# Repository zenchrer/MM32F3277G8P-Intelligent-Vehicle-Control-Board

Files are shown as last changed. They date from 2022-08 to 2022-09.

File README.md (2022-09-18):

# MM32F3277G8P-Intelligent-Vehicle-Control-Board

## 已添加[Sbus解析例程](https://github.com/zenchrer/MM32-Sbus-Demo.git)<br>
8/31/2022 9:24:01 PM <br>
&nbsp;&nbsp;&nbsp;&nbsp;本项目是2022年全国大学生智能车竞赛平衡信标组桂林信息科技学院Tornado(队)的硬件开源;
在一块PCB上集成了电机驱动以及其它外设接口,基本满足平衡信标组的功能需求,引脚大部分兼容某飞科技的开源程序,某飞的代码虽然有些BUG,但是大体方便可靠(个人认为比隔壁lq的好);电源部分设计参考了2021年立创开源广场moximoxi大佬的开源硬件:[传送门](https://oshwhub.com/moximoxi/shuang-jum3_mini)<br>

***
### 主要特点
+ 主控采用了灵动微电子MM32F3277G8P作为MCU;<br>
+ 电机驱动使用之前开源的EG3013栅极驱动以及N-Channel Mosfet;<br>
+ 预留S-bus接口,方便老车退役改成遥控车;(bushi)<br>
+ 预留并口屏,理论上相比SPI屏幕刷新更快,节约CPU时间;
+ 使用开源EDA软件Kicad6.0.2绘制;
***
### 开发者
组织：桂林信息科技学院 通信创新实践基地<br>
作者：zenchrer [邮箱](zenchrer@qq.com)
***

### 外观
PCB正面

安装图

安装图
***

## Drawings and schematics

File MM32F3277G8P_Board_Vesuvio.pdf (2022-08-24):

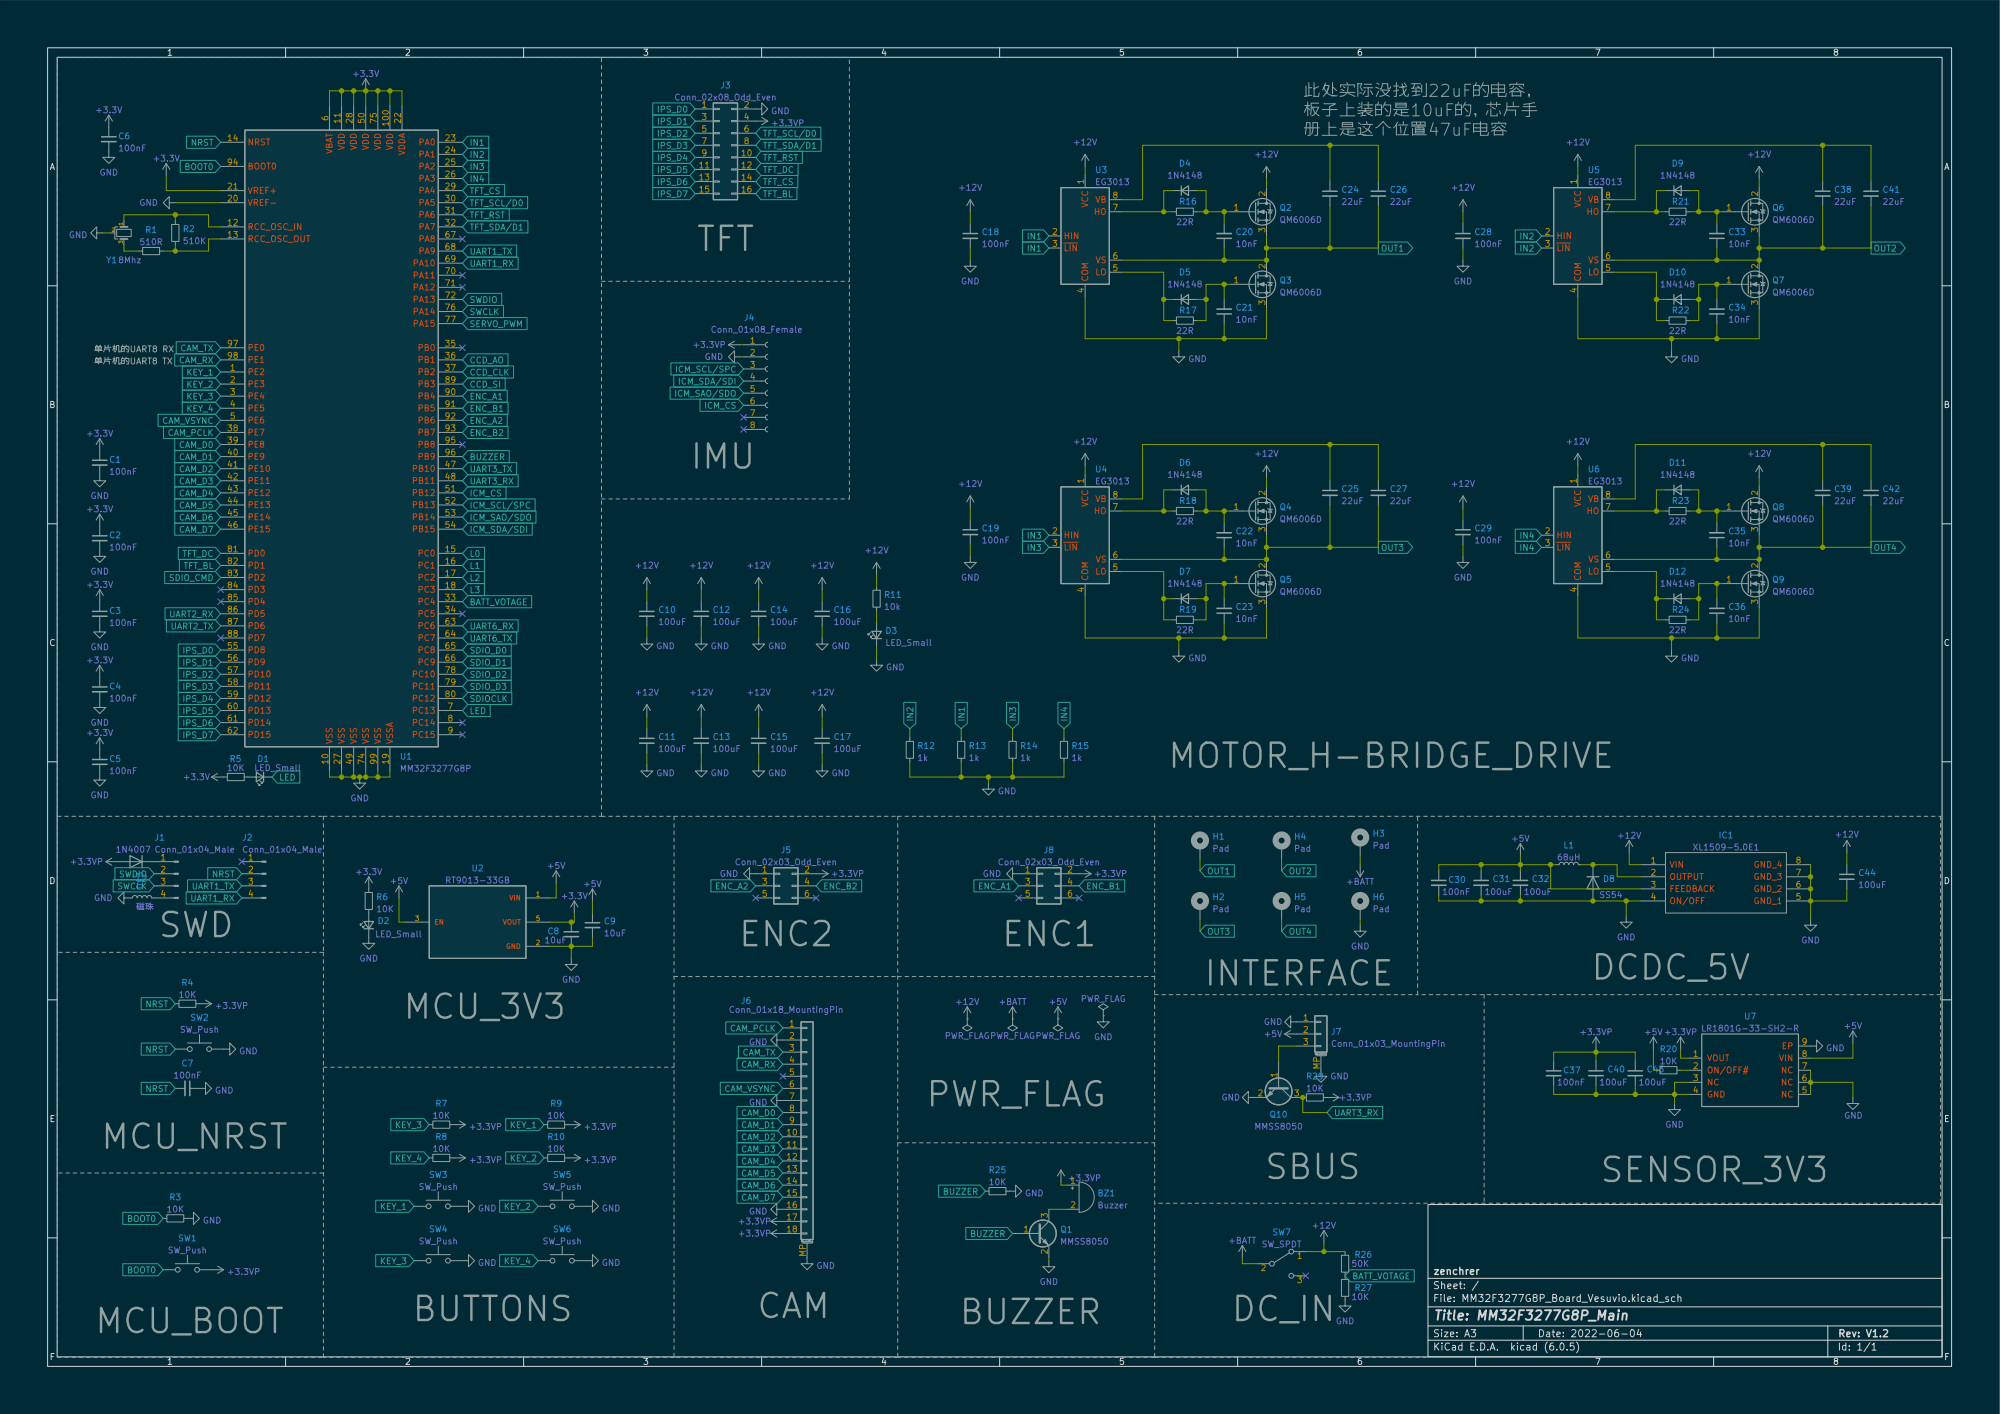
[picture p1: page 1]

þÿkdY[ž–El¡b~R022uFv„u5[¹ÿ þÿg•[PN

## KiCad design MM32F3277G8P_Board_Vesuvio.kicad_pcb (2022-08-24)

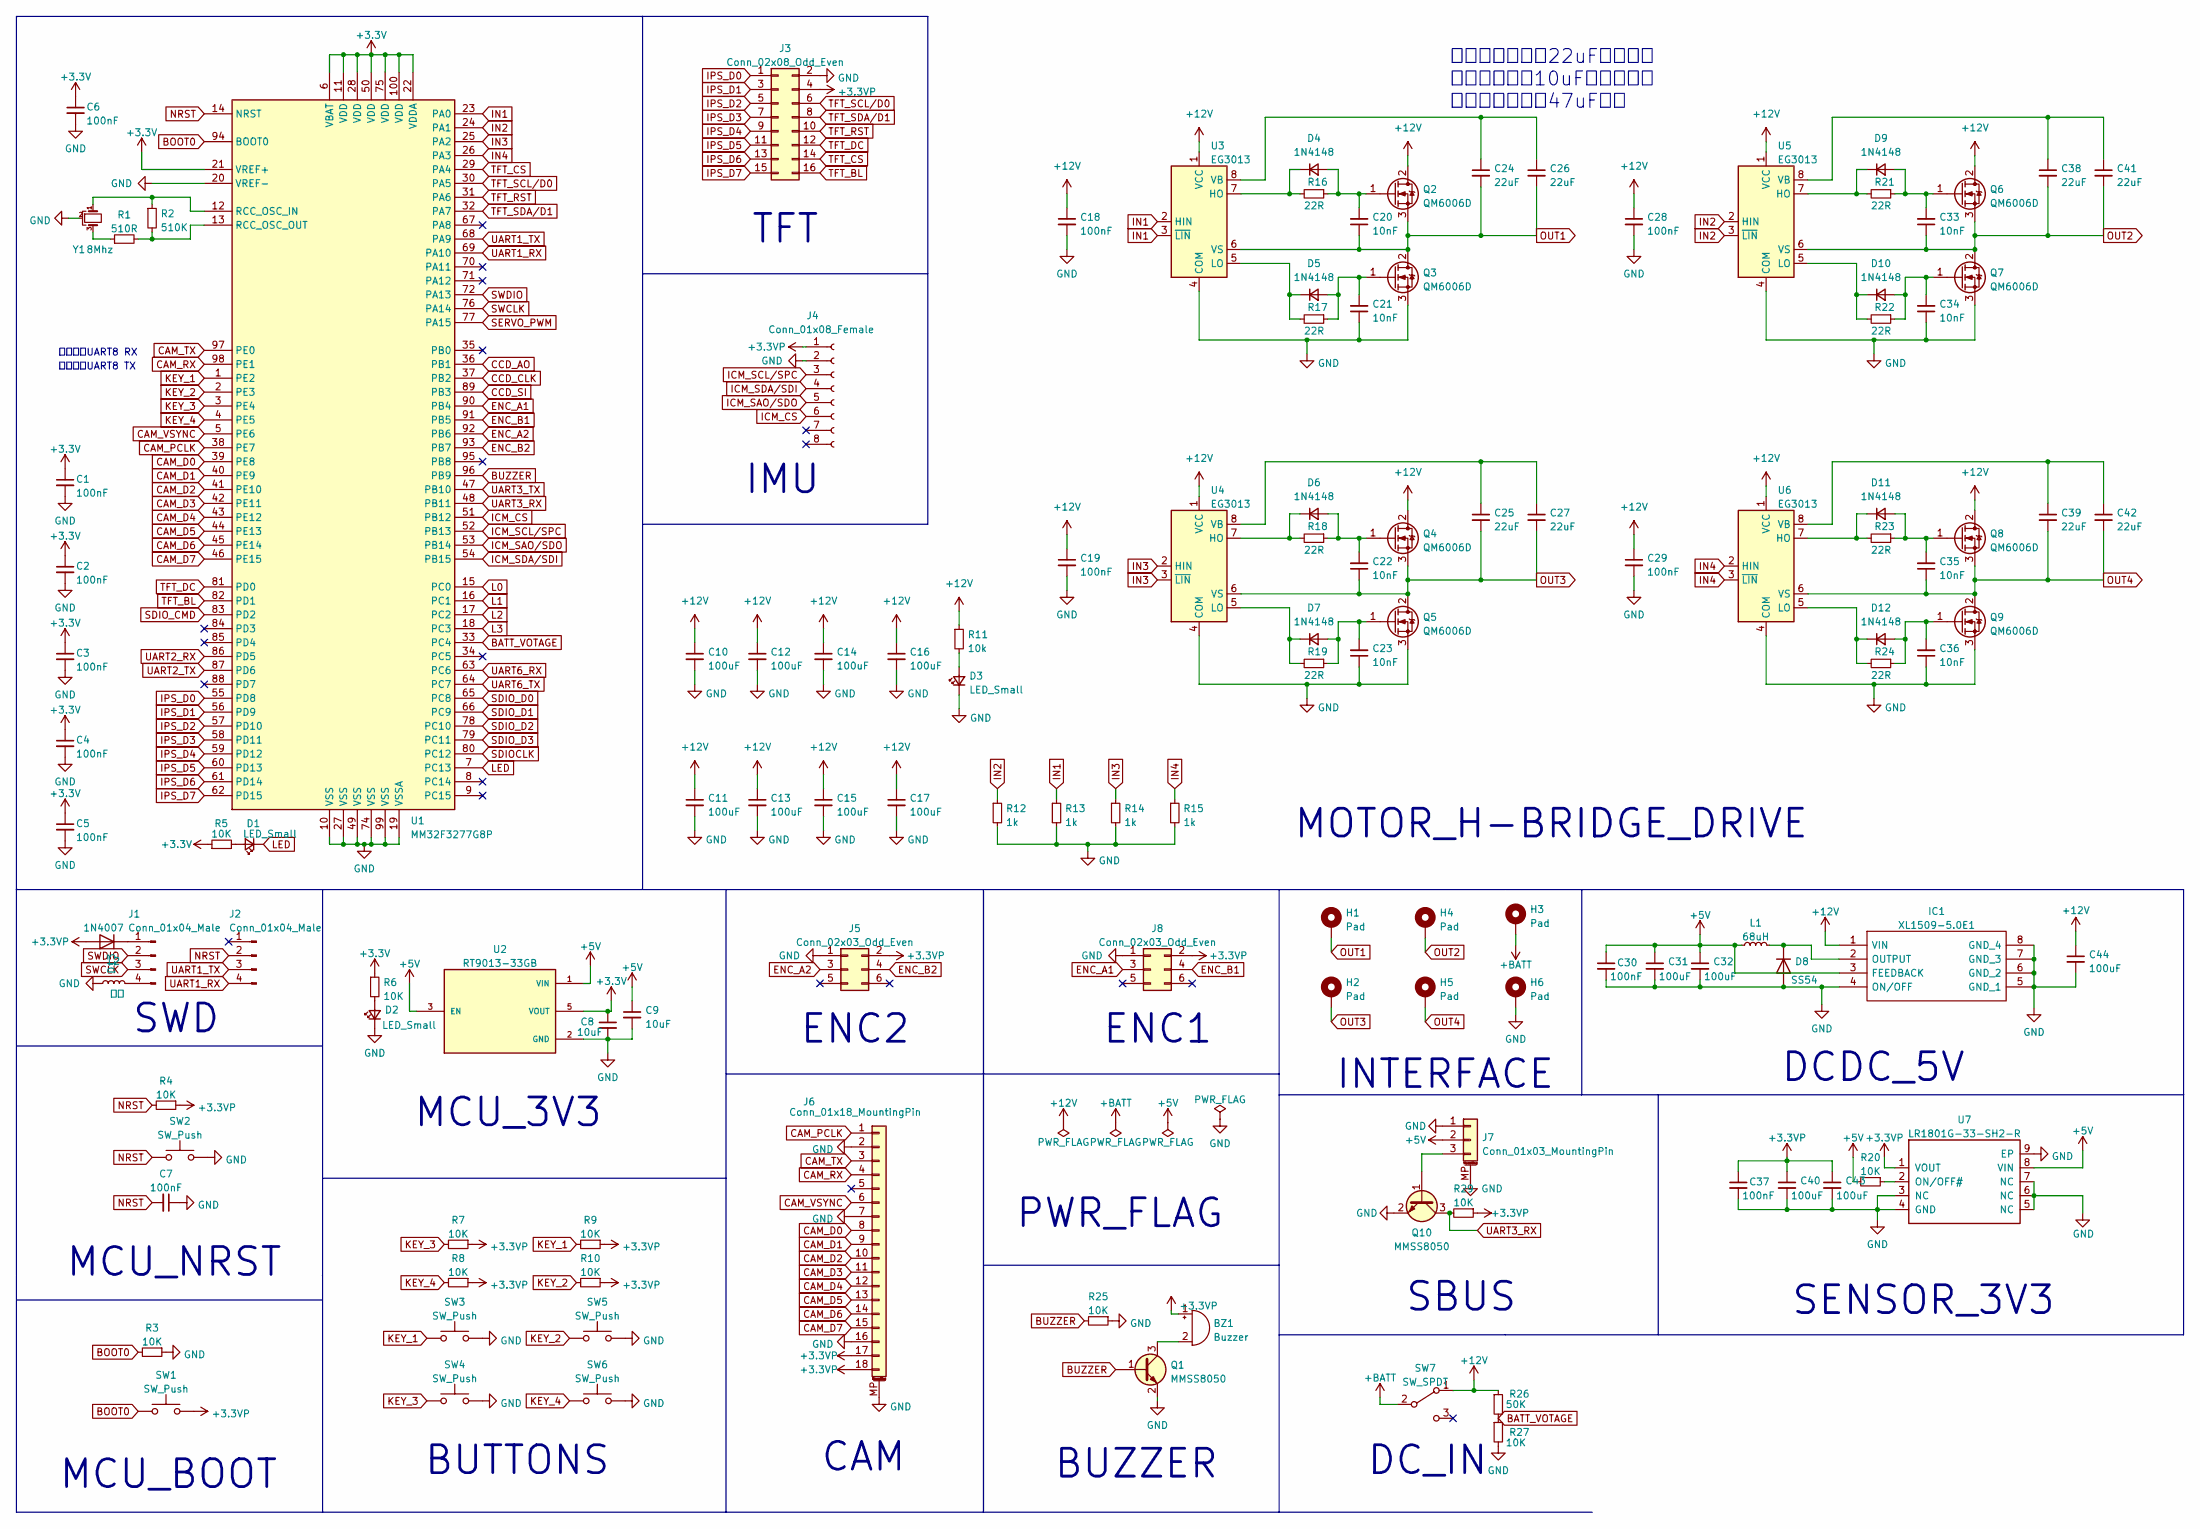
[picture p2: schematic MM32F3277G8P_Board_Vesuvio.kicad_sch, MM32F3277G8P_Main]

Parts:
BZ1: Buzzer; MagneticBuzzer_PUI_AT-0927-TT-6-R
C1, C2, C3, C4, C5, C6, C7, C18, C19, C28, C29, C30, C37: 100nF; C_0603_1608Metric
C8, C9: 10uF; C_0805_2012Metric
C10, C11, C12, C13, C14, C15, C16, C17, C31, C32, C40, C43, C44: 100uF; C_1210_3225Metric
C20, C21, C22, C23, C33, C34, C35, C36: 10nF; C_0402_1005Metric
C24, C25, C26, C27, C38, C39, C41, C42: 22uF; C_0805_2012Metric
D1, D2, D3: LED_Small; LED_0603_1608Metric
D4, D5, D6, D7, D9, D10, D11, D12: 1N4148; D_SOD-123
D8: SS54; D_SMA
D13: 1N4007; D_SMA
H1, H2, H4, H5: Pad; MountingHole_2.2mm_M2_Pad_Via
H3, H6: Pad; MountingHole_2.5mm_Pad_Via
IC1: XL1509-5.0E1; SOIC-8_3.9x4.9mm_P1.27mm; Manufacturer_Part_Number XL1509-5.0E1
J1, J2: Conn_01x04_Male; PinHeader_1x04_P2.54mm_Vertical
J3: Conn_02x08_Odd_Even; PinHeader_2x08_P2.54mm_Vertical
J4: Conn_01x08_Female; PinHeader_1x08_P2.54mm_Vertical
J5, J8: Conn_02x03_Odd_Even; IDC-Header_2x03_P2.54mm_Vertical
J6: Conn_01x18_MountingPin; TE_1-1734839-8_1x18-1MP_P0.5mm_Horizontal
J7: Conn_01x03_MountingPin; JST_SH_SM03B-SRSS-TB_1x03-1MP_P1.00mm_Horizontal
L1: 68uH; L_7.3x7.3_H3.5
L2: 磁珠; Fuse_0805_2012Metric
Q1, Q10: MMSS8050; SOT-23
Q2, Q3, Q4, Q5, Q6, Q7, Q8, Q9: QM6006D; TO-252-2
R1: 510R; R_0603_1608Metric
R2: 510K; R_0603_1608Metric
R3, R4, R5, R6, R7, R8, R9, R10, R20, R25, R27, R29: 10K; R_0603_1608Metric
R11: 10k; R_0603_1608Metric
R12, R13, R14, R15: 1k; R_0603_1608Metric
R16, R17, R18, R19, R21, R22, R23, R24: 22R; R_0402_1005Metric
R26: 50K; R_0603_1608Metric
SW1, SW2, SW3, SW4, SW5, SW6: SW_Push; SW_SPST_PTS810
SW7: SW_SPDT; MTS102
U1: MM32F3277G8P; LQFP-100_14x14mm_P0.5mm
U2: RT9013-33GB; SOT-23-5; PARTREV Aprill 2011
U3, U4, U5, U6: EG3013; SOIC-8_3.9x4.9mm_P1.27mm
U7: LR1801G-33-SH2-R; HSOP-8-1EP_3.9x4.9mm_P1.27mm_EP2.3x2.3mm_ThermalVias
Y1: 8Mhz; Resonator_SMD_Murata_CSTxExxV-3Pin_3.0x1.1mm

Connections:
+3.3VP: BZ1.1 (-), C37.1, C40.1, C43.1, D13.2 (A), J3.4, J4.1, J5.2, J6.17, J6.18, J8.2, R4.1, R7.1, R8.1, R9.1, R10.1, R29.1, SW1.2, U7.1 (VOUT)
+3V3: C1.1, C2.1, C3.1, C4.1, C5.1, C6.1, C8.1, R5.1, R6.1, U1.6 (VBAT), U1.11 (VDD), U1.21 (VREF+), U1.22 (VDDA), U1.28 (VDD), U1.50 (VDD), U1.75 (VDD), U1.100 (VDD), U2.5 (VOUT)
+5V: C9.1, C30.1, C31.1, C32.1, IC1.3 (FEEDBACK), J7.2, L1.1, R20.2, U2.1 (VIN), U2.3 (EN), U7.8 (VIN)
+12V: C10.1, C11.1, C12.1, C13.1, C14.1, C15.1, C16.1, C17.1, C18.1, C19.1, C28.1, C29.1, C44.1, IC1.1 (VIN), Q2.2 (D), Q4.2 (D), Q6.2 (D), Q8.2 (D), R11.1, R26.1, SW7.1 (A), U3.1 (VCC), U4.1 (VCC), U5.1 (VCC), U6.1 (VCC)
+BATT: H3.1, SW7.2 (B)
BATT_VOTAGE: R26.2, R27.1, U1.33 (PC4)
BOOT0: R3.2, SW1.1, U1.94 (BOOT0)
BUZZER: Q1.1 (B), R25.2, U1.96 (PB9)
CAM_D0: J6.8, U1.39 (PE8)
CAM_D1: J6.9, U1.40 (PE9)
CAM_D2: J6.10, U1.41 (PE10)
CAM_D3: J6.11, U1.42 (PE11)
CAM_D4: J6.12, U1.43 (PE12)
CAM_D5: J6.13, U1.44 (PE13)
CAM_D6: J6.14, U1.45 (PE14)
CAM_D7: J6.15, U1.46 (PE15)
CAM_PCLK: J6.1, U1.38 (PE7)
CAM_RX: J6.4, U1.98 (PE1)
CAM_TX: J6.3, U1.97 (PE0)
CAM_VSYNC: J6.6, U1.5 (PE6)
CCD_AO: U1.36 (PB1)
CCD_CLK: U1.37 (PB2)
CCD_SI: U1.89 (PB3)
ENC_A1: J8.3, U1.90 (PB4)
ENC_A2: J5.3, U1.92 (PB6)
ENC_B1: J8.4, U1.91 (PB5)
ENC_B2: J5.4, U1.93 (PB7)
GND: C1.2, C2.2, C3.2, C4.2, C5.2, C6.2, C7.1, C8.2, C9.2, C10.2, C11.2, C12.2, C13.2, C14.2, C15.2, C16.2, C17.2, C18.2, C19.2, C21.1, C23.1, C28.2, C29.2, C30.2, C31.2, C32.2, C34.1, C36.1, C37.2, C40.2, C43.2, C44.2, D2.1 (K), D3.1 (K), D8.2 (A), H6.1, IC1.4 (ON/OFF), IC1.5 (GND_1), IC1.6 (GND_2), IC1.7 (GND_3), IC1.8 (GND_4), J3.2, J4.2, J5.1, J6.2, J6.7, J6.16, J6.MP (MountPin), J7.1, J7.MP (MountPin), J8.1, L2.1, Q1.2 (E), Q3.3 (S), Q5.3 (S), Q7.3 (S), Q9.3 (S), Q10.2 (E), R3.1, R12.2, R13.2, R14.2, R15.2, R25.1, R27.2, SW2.2, SW3.2, SW4.2, SW5.2, SW6.2, U1.10 (VSS), U1.19 (VSSA), U1.20 (VREF-), U1.27 (VSS), U1.49 (VSS), U1.74 (VSS), U1.99 (VSS), U2.2 (GND), U3.4 (COM), U4.4 (COM), U5.4 (COM), U6.4 (COM), U7.3 (NC), U7.4 (GND), U7.5 (NC), U7.6 (NC), U7.7 (NC), U7.9 (EP), Y1.2
ICM_CS: J4.6, U1.51 (PB12)
ICM_SAO/SDO: J4.5, U1.53 (PB14)
ICM_SCL/SPC: J4.3, U1.52 (PB13)
ICM_SDA/SDI: J4.4, U1.54 (PB15)
IN1: R13.1, U1.23 (PA0), U3.2 (HIN), U3.3 (~LIN)
IN2: R12.1, U1.24 (PA1), U5.2 (HIN), U5.3 (~LIN)
IN3: R14.1, U1.25 (PA2), U4.2 (HIN), U4.3 (~LIN)
IN4: R15.1, U1.26 (PA3), U6.2 (HIN), U6.3 (~LIN)
IPS_D0: J3.1, U1.55 (PD8)
IPS_D1: J3.3, U1.56 (PD9)
IPS_D2: J3.5, U1.57 (PD10)
IPS_D3: J3.7, U1.58 (PD11)
IPS_D4: J3.9, U1.59 (PD12)
IPS_D5: J3.11, U1.60 (PD13)
IPS_D6: J3.13, U1.61 (PD14)
IPS_D7: J3.15, U1.62 (PD15)
KEY_1: R9.2, SW3.1, U1.1 (PE2)
KEY_2: R10.2, SW5.1, U1.2 (PE3)
KEY_3: R7.2, SW4.1, U1.3 (PE4)
KEY_4: R8.2, SW6.1, U1.4 (PE5)
L0: U1.15 (PC0)
L1: U1.16 (PC1)
L2: U1.17 (PC2)
L3: U1.18 (PC3)
LED: D1.1 (K), U1.7 (PC13)
NRST: C7.2, J2.2, R4.2, SW2.1, U1.14 (NRST)
unnamed: BZ1.2 (+), Q1.3 (C)
unnamed: C20.2, D4.2 (A), Q2.1 (G), R16.1
unnamed: C21.2, D5.2 (A), Q3.1 (G), R17.1
unnamed: C22.2, D6.2 (A), Q4.1 (G), R18.1
unnamed: C23.2, D7.2 (A), Q5.1 (G), R19.1
unnamed: C24.1, C26.1, U3.8 (VB)
unnamed: C25.1, C27.1, U4.8 (VB)
unnamed: C33.2, D9.2 (A), Q6.1 (G), R21.1
unnamed: C34.2, D10.2 (A), Q7.1 (G), R22.1
unnamed: C35.2, D11.2 (A), Q8.1 (G), R23.1
unnamed: C36.2, D12.2 (A), Q9.1 (G), R24.1
unnamed: C38.1, C41.1, U5.8 (VB)
unnamed: C39.1, C42.1, U6.8 (VB)
unnamed: D1.2 (A), R5.2
unnamed: D2.2 (A), R6.2
unnamed: D3.2 (A), R11.2
unnamed: D4.1 (K), R16.2, U3.7 (HO)
unnamed: D5.1 (K), R17.2, U3.5 (LO)
unnamed: D6.1 (K), R18.2, U4.7 (HO)
unnamed: D7.1 (K), R19.2, U4.5 (LO)
unnamed: D8.1 (K), IC1.2 (OUTPUT), L1.2
unnamed: D9.1 (K), R21.2, U5.7 (HO)
unnamed: D10.1 (K), R22.2, U5.5 (LO)
unnamed: D11.1 (K), R23.2, U6.7 (HO)
unnamed: D12.1 (K), R24.2, U6.5 (LO)
unnamed: D13.1 (K), J1.1
unnamed: J1.4, L2.2
unnamed: J7.3, Q10.1 (B)
unnamed: R1.1, Y1.3
unnamed: R1.2, R2.2, U1.13 (RCC_OSC_OUT)
unnamed: R2.1, U1.12 (RCC_OSC_IN), Y1.1
unnamed: R20.1, U7.2 (ON/OFF#)
OUT1: C20.1, C24.2, C26.2, H1.1, Q2.3 (S), Q3.2 (D), U3.6 (VS)
OUT2: C33.1, C38.2, C41.2, H4.1, Q6.3 (S), Q7.2 (D), U5.6 (VS)
OUT3: C22.1, C25.2, C27.2, H2.1, Q4.3 (S), Q5.2 (D), U4.6 (VS)
OUT4: C35.1, C39.2, C42.2, H5.1, Q8.3 (S), Q9.2 (D), U6.6 (VS)
SDIOCLK: U1.80 (PC12)
SDIO_CMD: U1.83 (PD2)
SDIO_D0: U1.65 (PC8)
SDIO_D1: U1.66 (PC9)
SDIO_D2: U1.78 (PC10)
SDIO_D3: U1.79 (PC11)
SERVO_PWM: U1.77 (PA15)
SWCLK: J1.3, U1.76 (PA14)
SWDIO: J1.2, U1.72 (PA13)
TFT_BL: J3.16, U1.82 (PD1)
TFT_CS: J3.14, U1.29 (PA4)
TFT_DC: J3.12, U1.81 (PD0)
TFT_RST: J3.10, U1.31 (PA6)
TFT_SCL/D0: J3.6, U1.30 (PA5)
TFT_SDA/D1: J3.8, U1.32 (PA7)
UART1_RX: J2.4, U1.69 (PA10)
UART1_TX: J2.3, U1.68 (PA9)
UART2_RX: U1.86 (PD5)
UART2_TX: U1.87 (PD6)
UART3_RX: Q10.3 (C), R29.2, U1.48 (PB11)
UART3_TX: U1.47 (PB10)
UART6_RX: U1.63 (PC6)
UART6_TX: U1.64 (PC7)

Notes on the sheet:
SENSOR_3V3
MCU_3V3
IMU
PWR_FLAG
DC_IN
SWD
ENC1
MOTOR_H-BRIDGE_DRIVE
MCU_NRST
单片机的UART8 TX
SBUS
BUTTONS
ENC2
此处实际没找到22uF的电容， 板子上装的是10uF的，芯片手 册上是这个位置47uF电容
单片机的UART8 RX
MCU_BOOT
INTERFACE
BUZZER
DCDC_5V
CAM
TFT

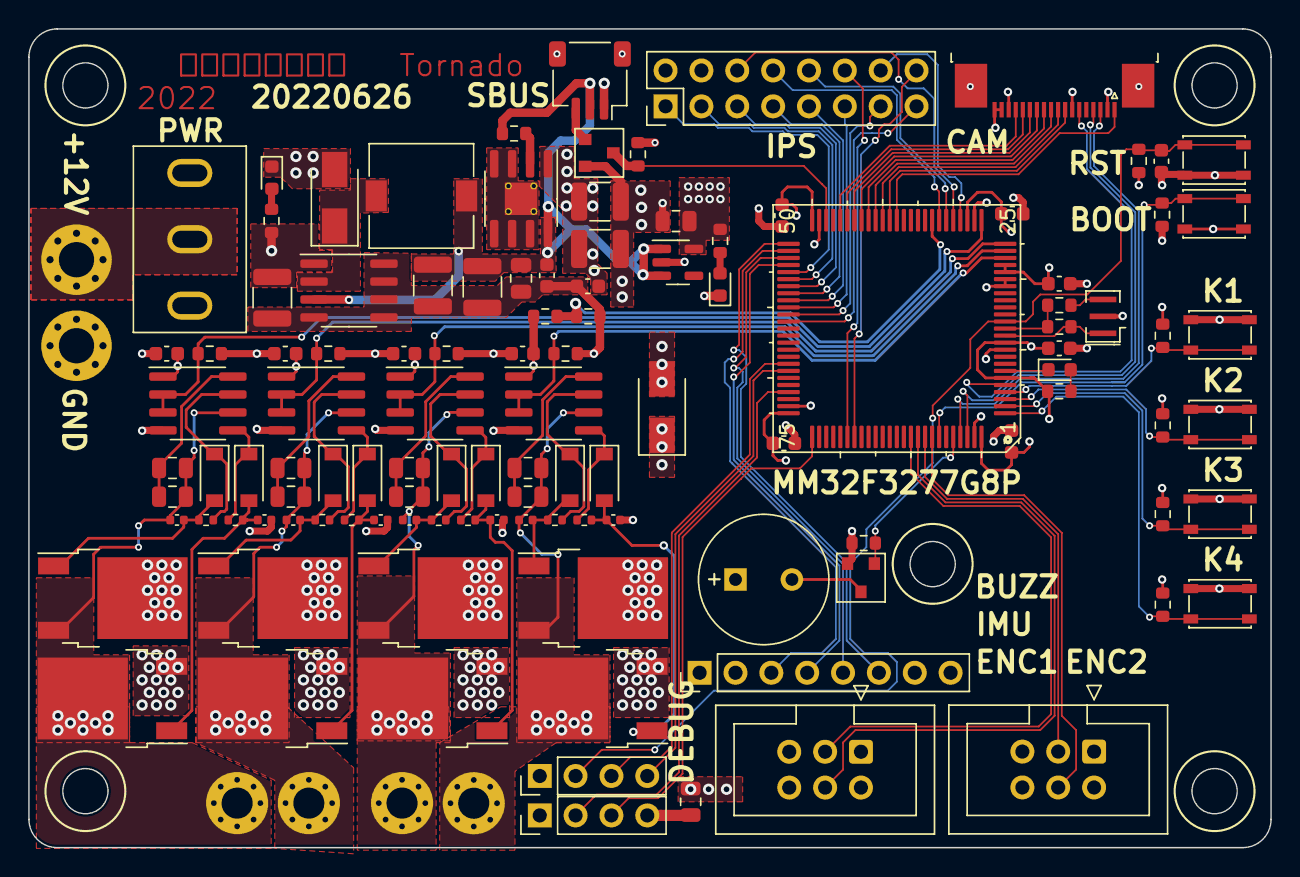
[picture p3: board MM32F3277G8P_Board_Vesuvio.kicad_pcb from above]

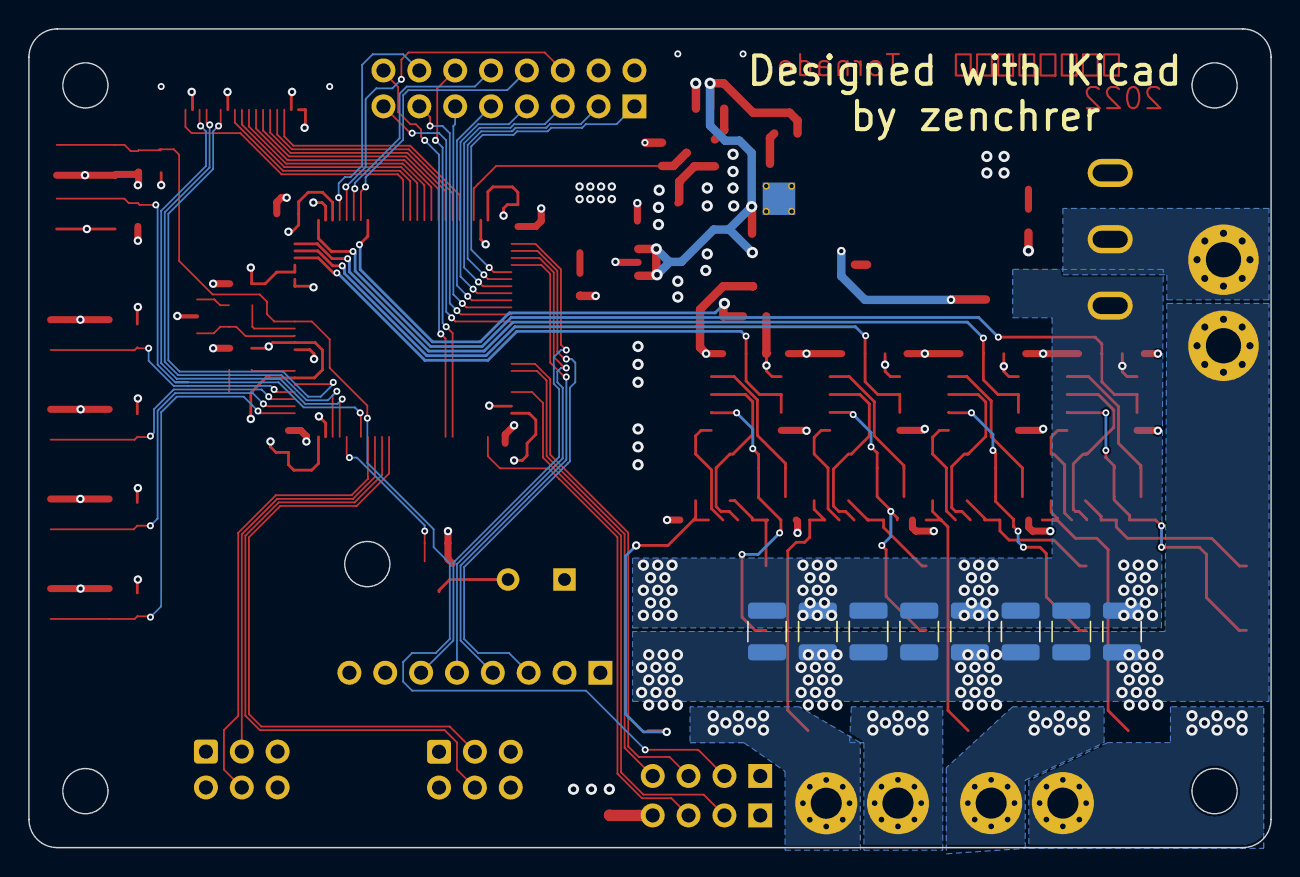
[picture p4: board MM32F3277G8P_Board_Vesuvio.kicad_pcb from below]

Board: 4 copper layers, 88.0 x 58.0 mm, 128 parts (8 on the bottom side), 94 nets.

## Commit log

2022-08-24 add pcb and sch
    [MM32F3277G8P_Board_Vesuvio.kicad_pcb, MM32F3277G8P_Board_Vesuvio.kicad_sch]
2022-08-27 添加Sbus 解析例程
2022-08-29 添加部分注释
2022-08-29 Sbus例程移除
2022-08-29 更细子仓库到主仓库代码库中
